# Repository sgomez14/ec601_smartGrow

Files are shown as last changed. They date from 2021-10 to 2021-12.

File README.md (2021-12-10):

# SmartGrow: Modular Smart Hydroponics System

## Problem:  Efficient Agriculture in a Worsening Climate
How can we efficiently bring agriculture indoors, so people can easily grow their own food?

## Solution
Take hydroponics, and make it smarter, scalable, and easily approachable.

## Users
Market: Scalable from a single person, to a  building, to a community.

## Societal Impact
Make self-sufficient farm more compact and accessible for urban communities.

Decreases food-waste, transit-fuel, land-use.

## Developers

| Name | Email |
| --- | --- |
| Santiago Gomez | santi09@bu.edu  |
| Ben Kuter | bmkuter@bu.edu  |
| Yuan Sui | suiyuan@bu.edu  |

## GrowPods

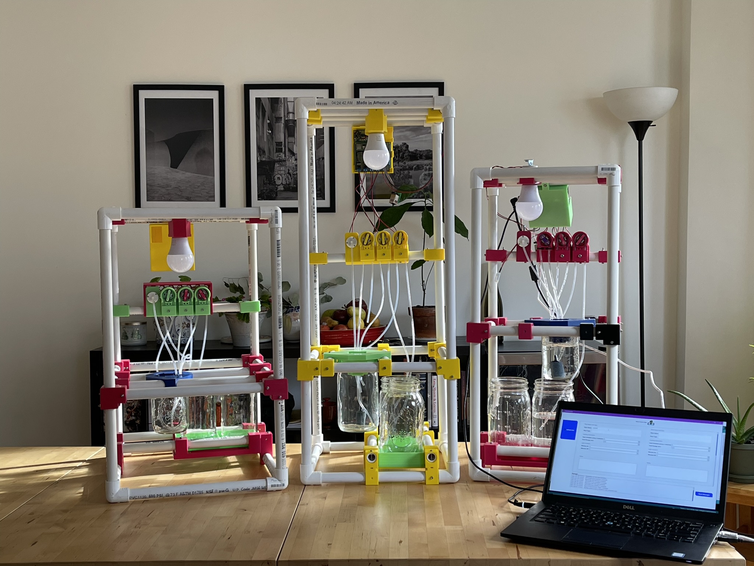
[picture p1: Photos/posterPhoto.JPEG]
GrowPods

Figure 1: Three Different Sized GrowPods

## GUI

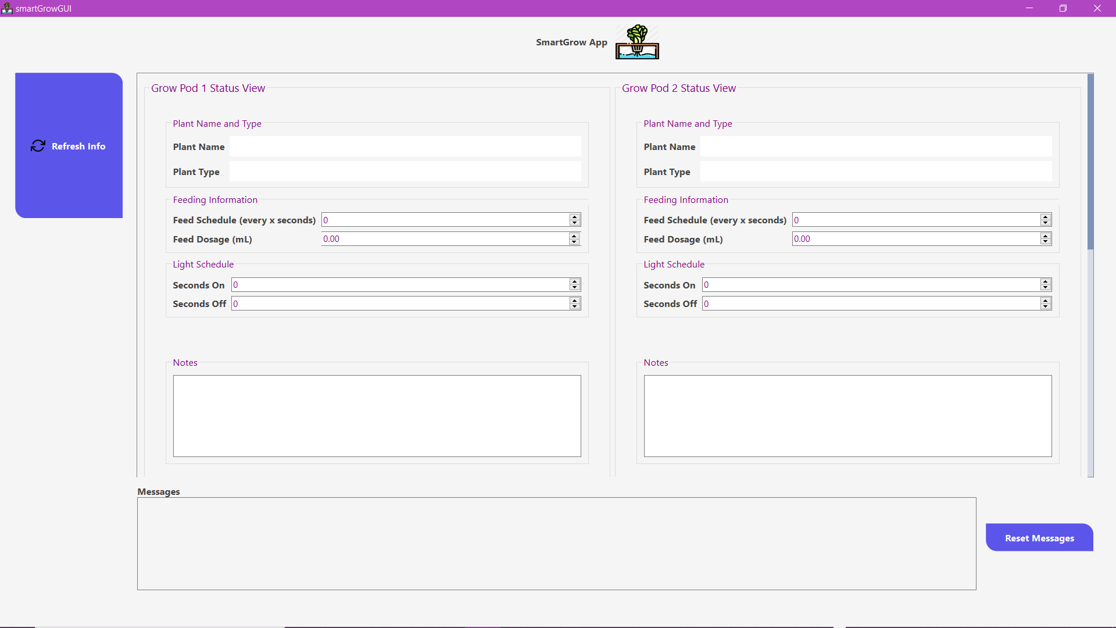
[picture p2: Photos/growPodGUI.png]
SmartGrow GUI

Figure 2: Smart GUI to Control GrowPods

## Functional Block Diagrams

### GrowPod Embedded System

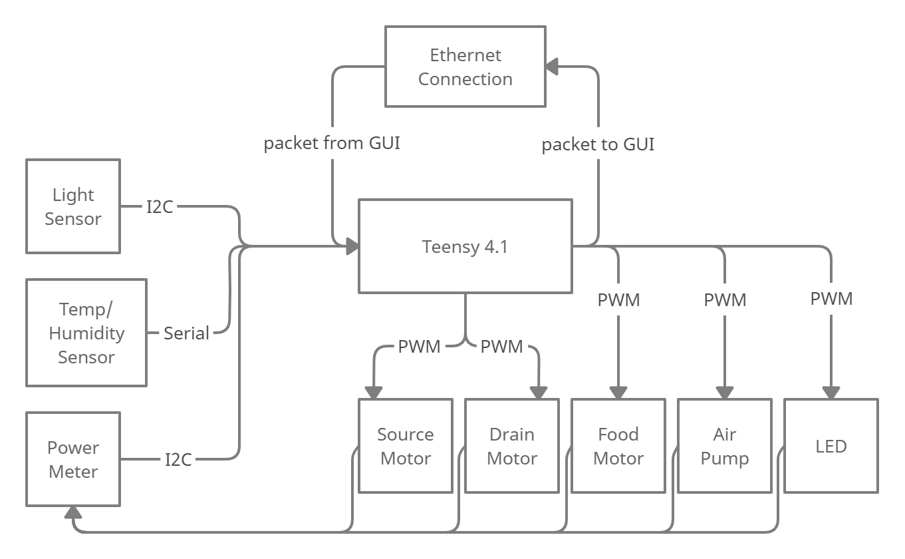
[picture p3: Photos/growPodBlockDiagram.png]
GrowPod Block Diagram

Figure 3: Block Diagram Explaining Embedded System Architecture

### UDP Communication Layer

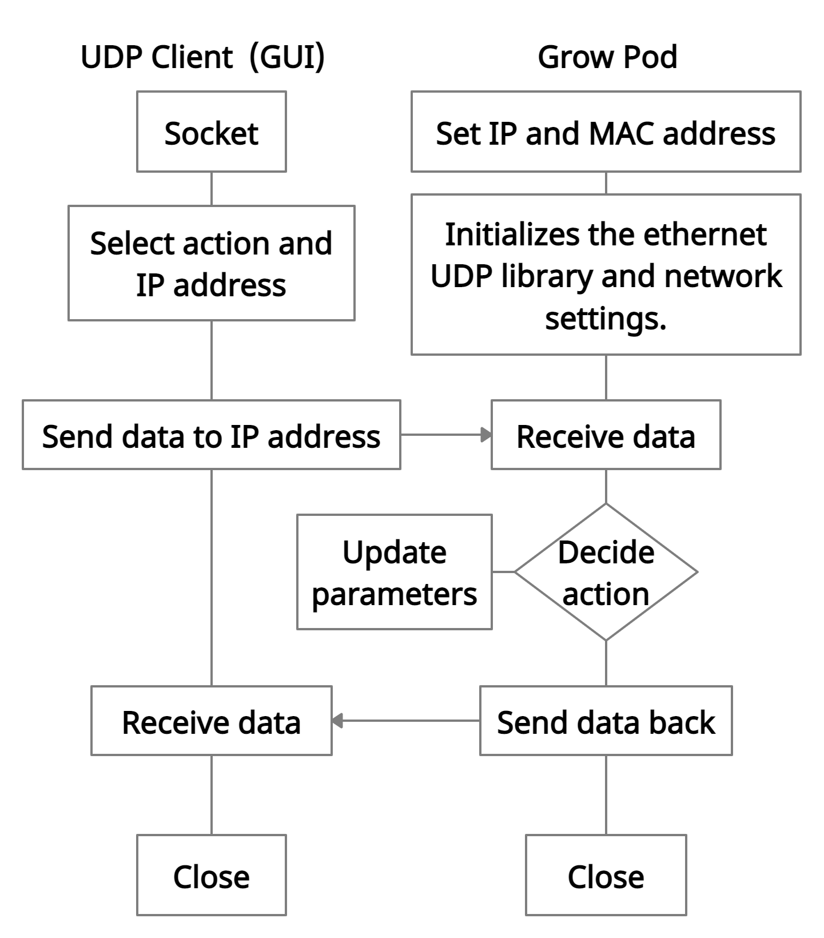
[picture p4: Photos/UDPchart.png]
UDP Block Diagram

Figure 4: Block Diagram Explaining UDP Communication Layer

## GrowPod Circuit

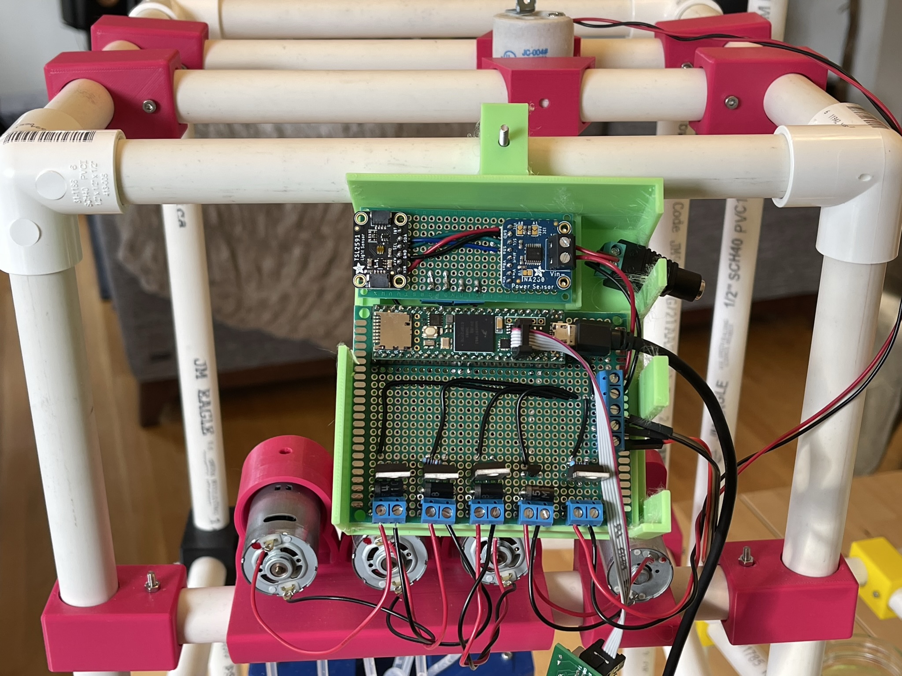
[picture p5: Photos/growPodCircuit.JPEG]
GrowPod Circuit Photo

Figure 5: Image of GrowPod Circuit

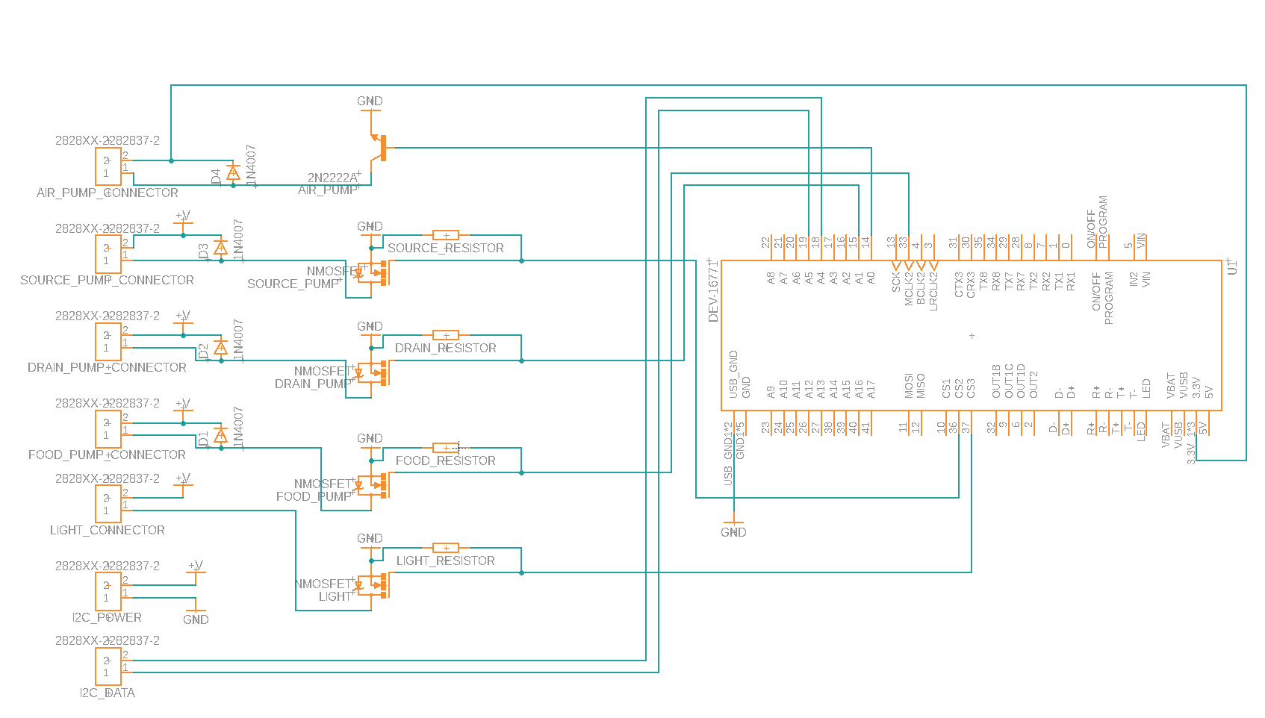
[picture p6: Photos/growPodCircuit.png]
GrowPod Circuit Diagram

Figure 6: Diagram of GrowPod Circuit

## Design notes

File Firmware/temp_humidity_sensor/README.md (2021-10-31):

# Temperature and Humidity Sensor README

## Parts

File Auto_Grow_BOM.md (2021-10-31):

**Benjamin Kuter**  
**EC601 - Fall 2021**  
**Automated Agricultural Grow System: Bill of Materials**  

<h2>pH Meter</h2>  
Probably one of the most expensive components that is the hardest to DIY, this costs ~$29 for V1 and ~$39 for V2. It is also fairly important to have for a hydroponics setup, since there is no soil to act as a buffer for the plant.  
*Link: https://www.dfrobot.com/product-1025.html*  

<h2>Teensy 4.1</h2>  
Brains of the operation. These are very powerful MCUs with very good support & programmability.  
*Link: https://www.pjrc.com/store/teensy41.html*  

<h2>Humidity & Temperature Sensor</h2>  
From Adafruit, the DHT22 is a low-cost digital temperature and humidity sensor. It can only poll data every couple of seconds, but for this application that is sufficient, especially considering the low price and ease of expanding larger modules with additional sensors.  
*Link: https://www.adafruit.com/product/385*  

<h2>Light Sensor</h2>  
VEML7700

<h2>Servos</h2>  
These are needed to open & close the drainage connections to each hydroponics unit, allowing water to be replaced within each module. The alternative would be another peristaltic pump, which may be too slow.  
*Link:  Product TBD*  

<h2>Peristaltic Liquid Pump</h2>
These will be used to safely (*following food safety regulations*) pump water from either the water reservoir to a module's hydroponics, or from the nutrient supply to the hydroponics chamber.    
*Link:  https://smile.amazon.com/gp/product/B01IUVHB8E/ref=ox_sc_saved_title_9?smid=A34K5WF5Z9R33P&psc=1*  
*Link: https://smile.amazon.com/gp/product/B08H1ZD5VZ/ref=ox_sc_saved_image_4?smid=A34K5WF5Z9R33P&psc=1*

<h2>Relays</h2>  
Numerous devices use 12v power, so a relay is needed to control these higher voltage devices.    
*Link:  https://smile.amazon.com/gp/product/B00KTELP3I/ref=ox_sc_saved_title_7?smid=A28RI4FXFS5SV8&psc=1*  

<h2>Grow Lights</h2>  
Once again, controlled via a relay. These could be replaced by higher quality alternatives, but for this project we are using standard A19 bulbs.  
*Link: https://smile.amazon.com/gp/product/B085ZVM2R7/ref=ox_sc_saved_image_2?smid=AWFJMAQAWVQZ0&psc=1*  
*Link: https://smile.amazon.com/gp/product/B07FMRLSWC/ref=ox_sc_saved_image_8?smid=A2C06C9V9JAET9&psc=1*  

<h2>HVAC</h2>  
This project assumes no odour control is needed. Airflow is still crucial for controlling humidity, temperature, and oxygen to root zones.  
*Link: TBD, probably computer fans I have around.*  

<h2>Humidifier</h2>
Exact product TBD, but something like this.  
*Link: https://smile.amazon.com/ToToT-5-Pack-Ultrasonic-Ceramics-Sealing/dp/B07RMX472R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*

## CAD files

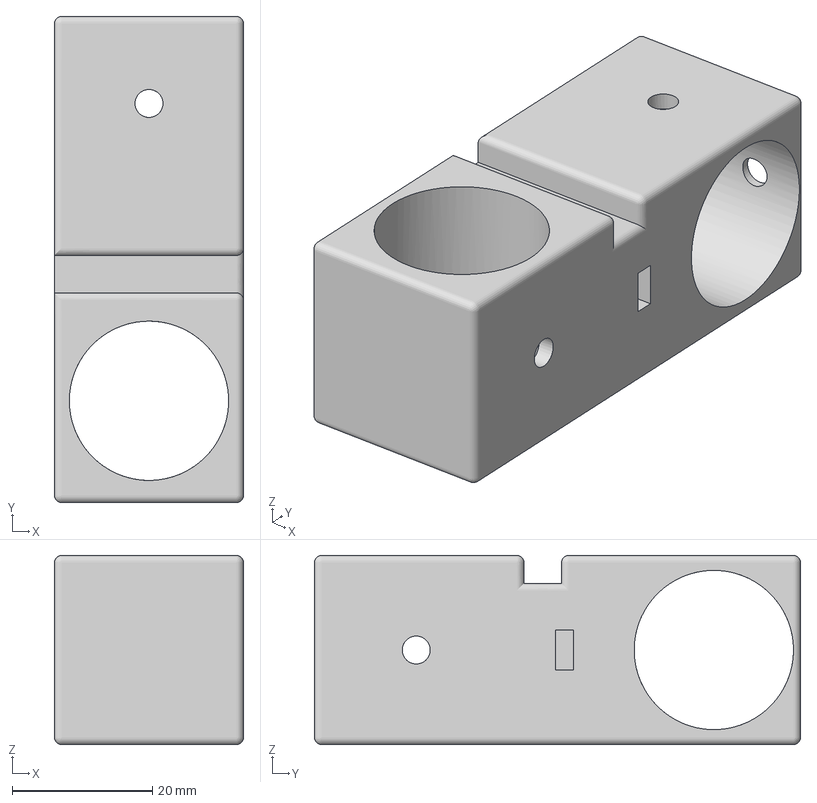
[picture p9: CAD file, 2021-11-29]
CAD/Stacked right.3mf
27.0 x 69.4 x 27.0 mm

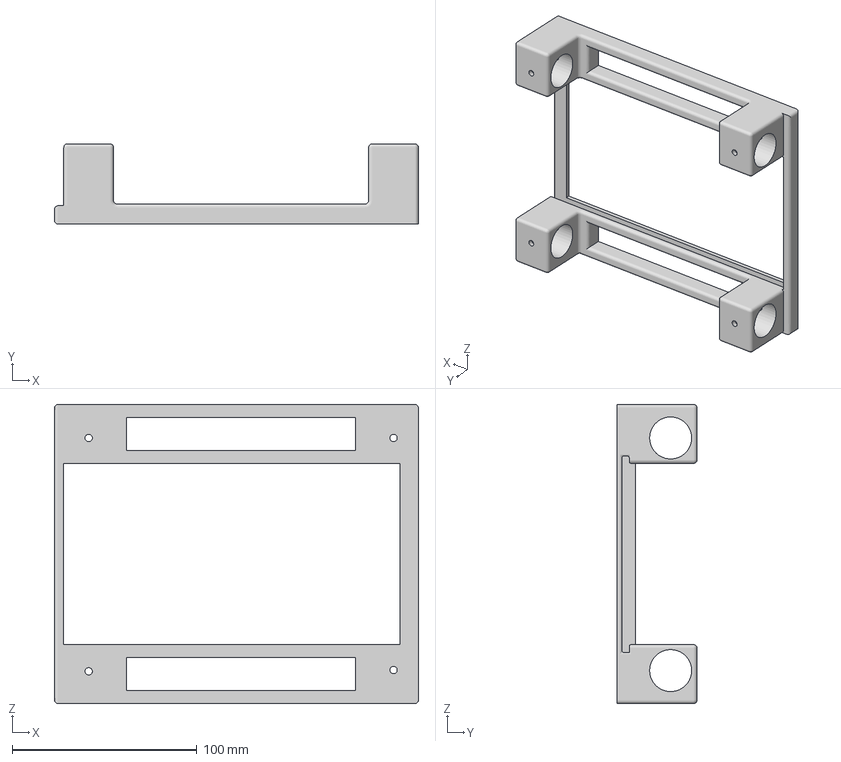
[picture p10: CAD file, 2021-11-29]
CAD/Bottom (1).3mf
197.0 x 43.5 x 162.0 mm

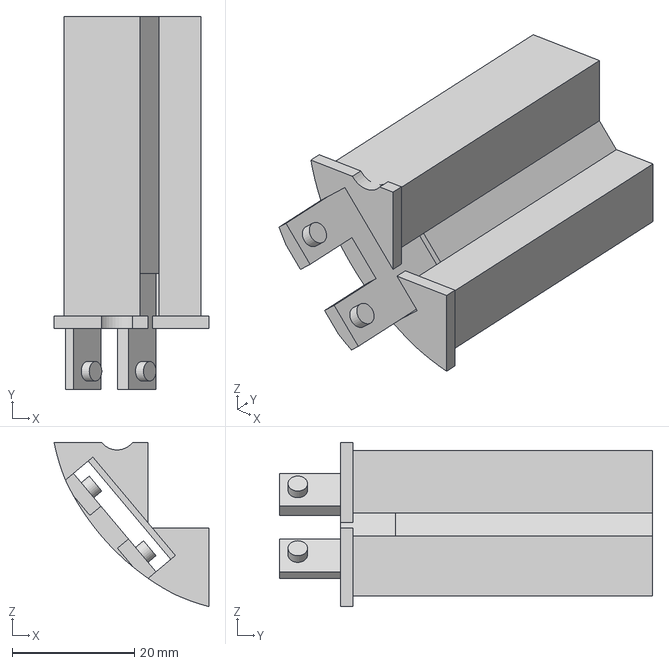
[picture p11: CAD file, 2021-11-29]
CAD/Water Sensor.3mf
25.3 x 61.0 x 26.9 mm

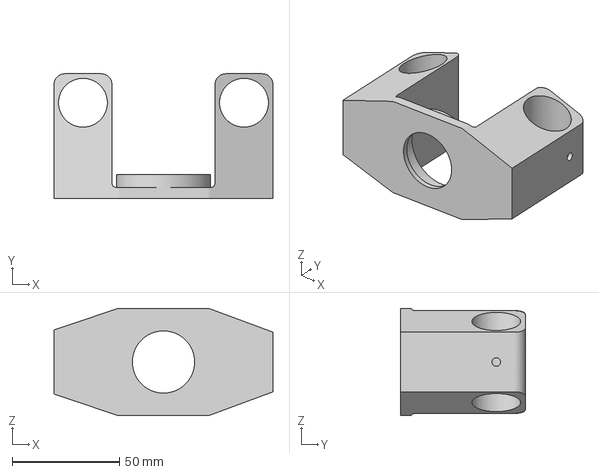
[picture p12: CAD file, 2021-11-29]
CAD/Light Fixture.3mf
102.0 x 58.0 x 50.0 mm

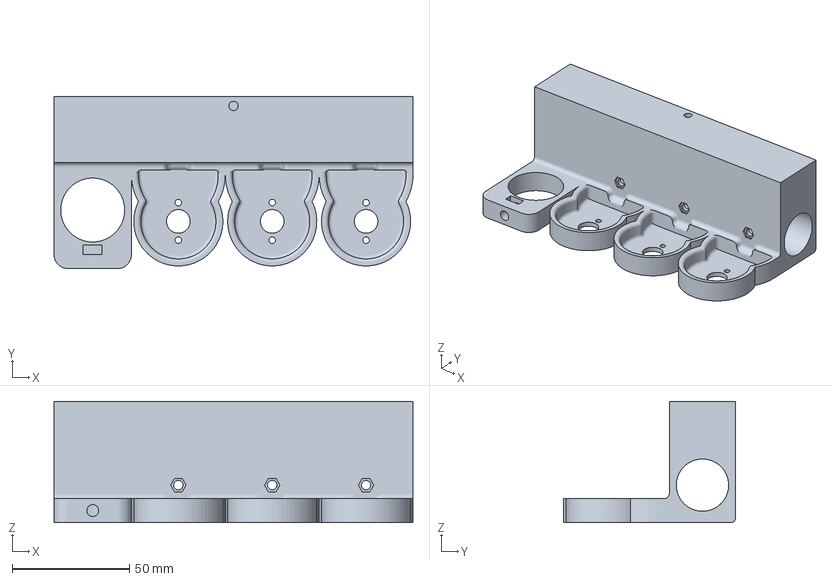
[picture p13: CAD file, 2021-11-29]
CAD/motor_mount.3mf
153.0 x 73.5 x 51.7 mm

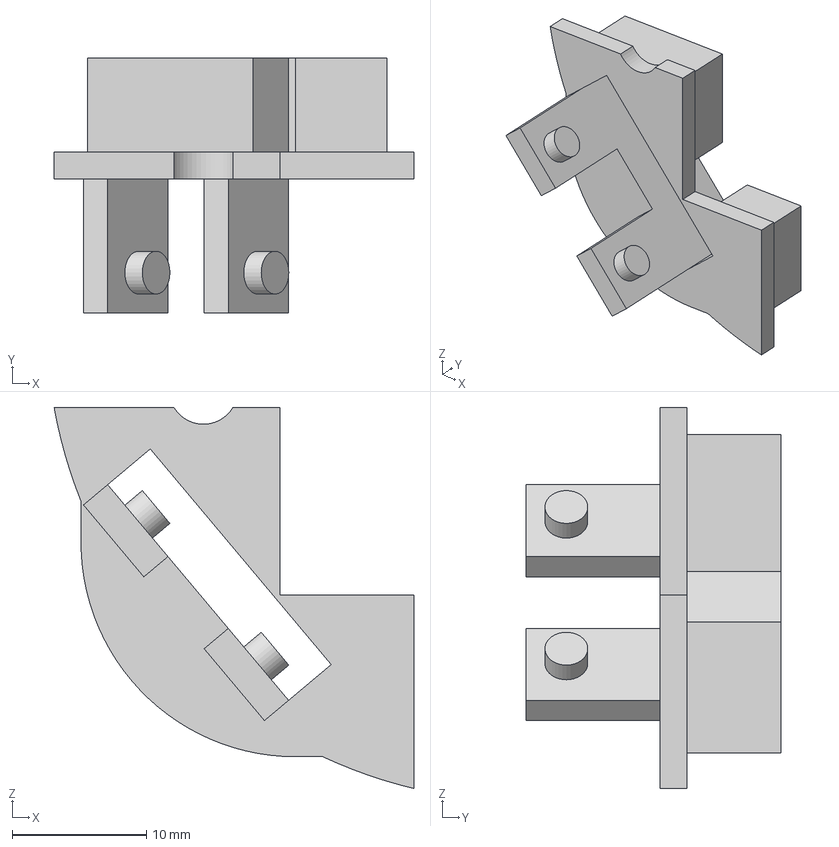
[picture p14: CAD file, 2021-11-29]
CAD/Water Sensor Block.3mf
26.8 x 19.0 x 28.4 mm

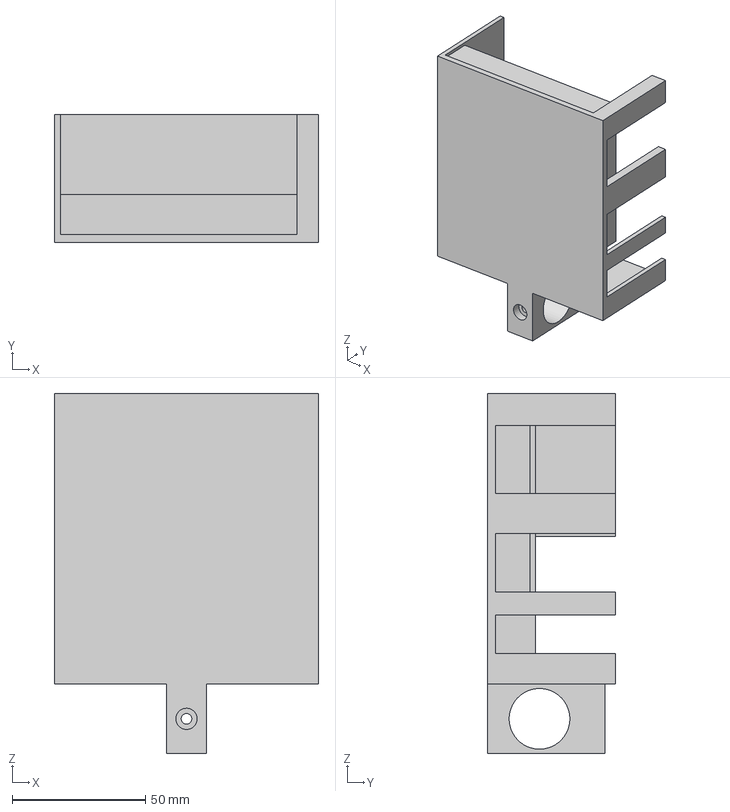
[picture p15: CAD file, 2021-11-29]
CAD/Body7.3mf
99.0 x 48.0 x 135.0 mm

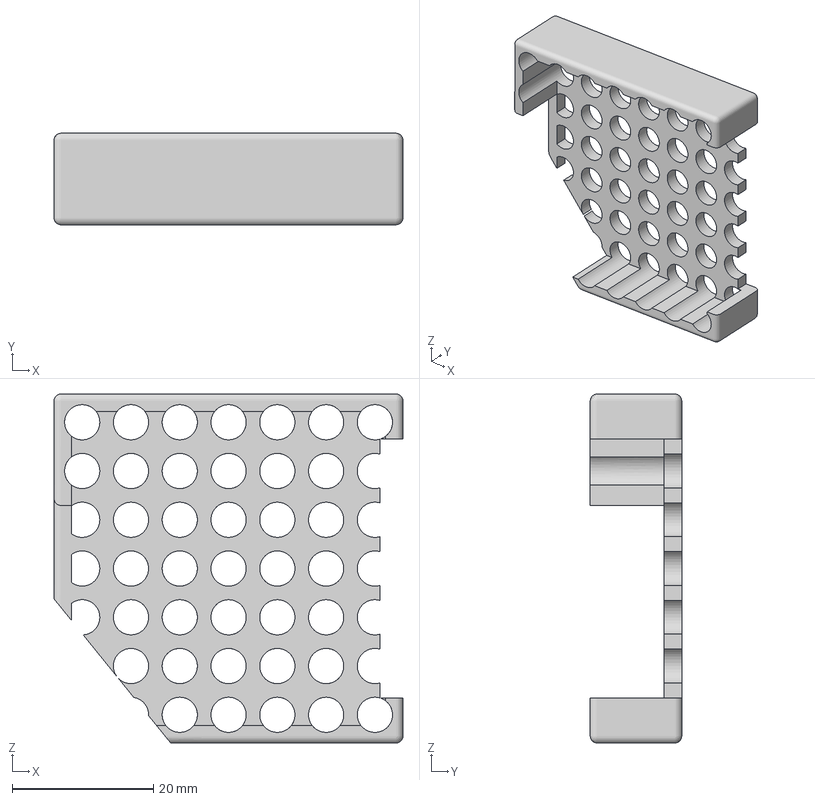
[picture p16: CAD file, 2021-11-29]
CAD/planter_lid.3mf
49.5 x 13.0 x 49.5 mm

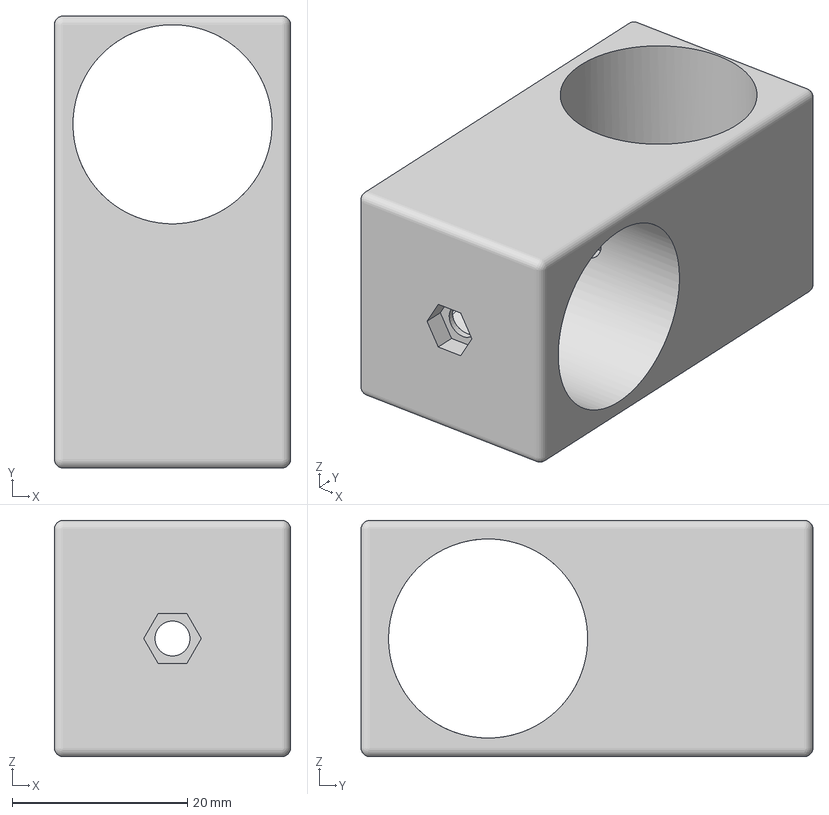
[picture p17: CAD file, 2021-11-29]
CAD/Stacked.3mf
27.0 x 51.6 x 27.0 mm

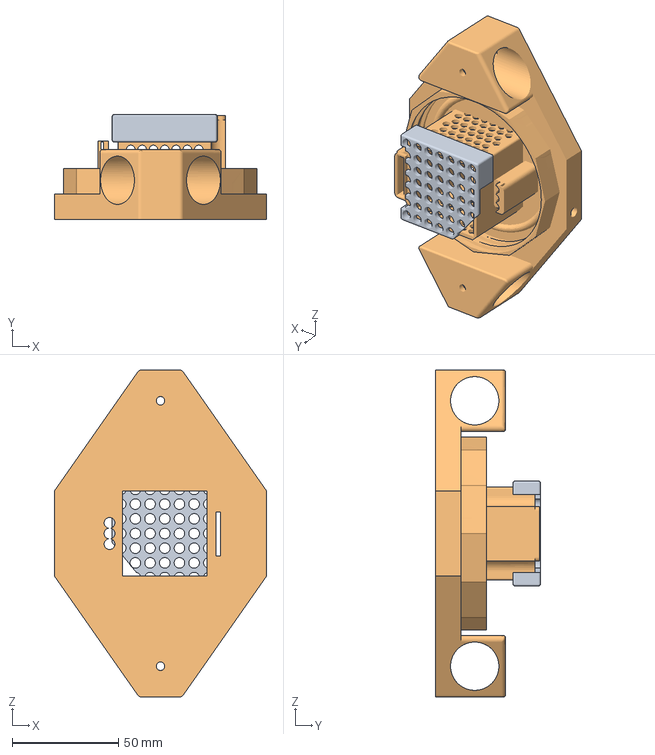
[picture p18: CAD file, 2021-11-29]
CAD/Planter.3mf
100.0 x 49.5 x 154.0 mm
planter

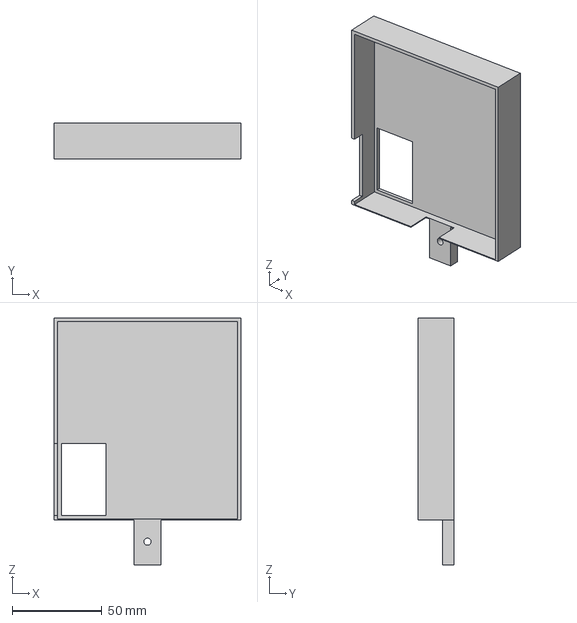
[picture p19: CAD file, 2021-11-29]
CAD/Top.3mf
104.0 x 20.0 x 137.5 mm

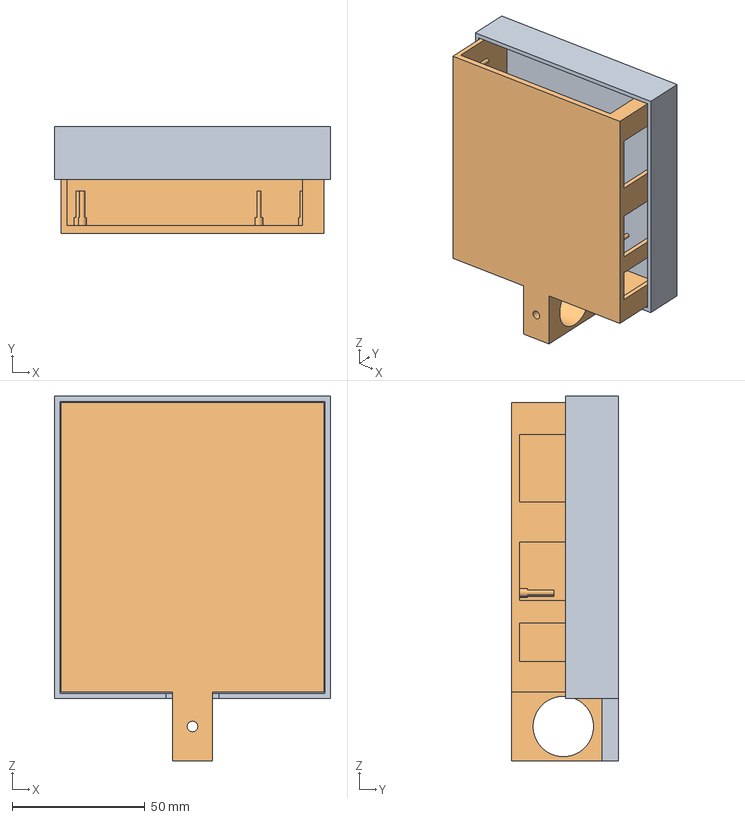
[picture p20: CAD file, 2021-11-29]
CAD/PCB case.3mf
104.0 x 40.2 x 137.5 mm

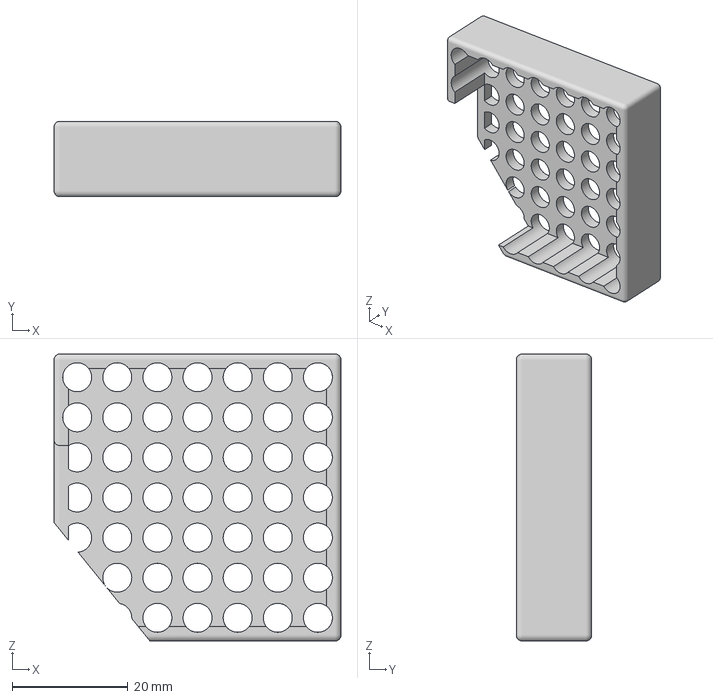
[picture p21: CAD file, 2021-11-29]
CAD/Grow Lid.3mf
49.5 x 13.0 x 49.5 mm

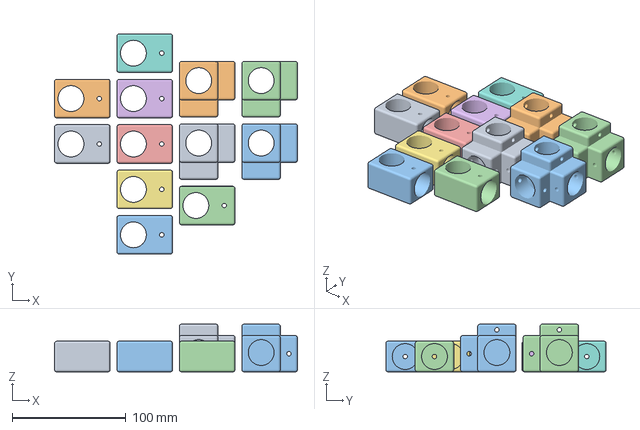
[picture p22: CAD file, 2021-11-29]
CAD/Tube arm.3mf
214.0 x 194.0 x 42.0 mm
Corner
Middle

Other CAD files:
CAD/Stacked left.3mf
CAD/Drawer.3mf
CAD/Flywheel.3mf
CAD/Body9.3mf
CAD/3mm x 4mm Adapter.3mf
CAD/4 Motor Mount.3mf
CAD/Air Pump Base.3mf
CAD/Balance Wheel.3mf
CAD/Base.3mf
CAD/Body8.3mf
CAD/Bottom Frame (2) (1).3mf
CAD/Bottom Frame (2).3mf
CAD/Bottom Frame Knurled.3mf
CAD/Bottom Wheel (2).3mf
CAD/Centrifugal Air Pump.3mf
CAD/Impeller.3mf
CAD/Middle.3mf
CAD/Motor Enclosure.3mf
CAD/Motor Mount V2.3mf
CAD/PVC jig.3mf
CAD/Planter.stl
CAD/Top Frame (2).3mf
CAD/Top Wheel (2) (1).3mf
CAD/Top Wheel (2).3mf
CAD/Tray.3mf
CAD/Water Pump.3mf
CAD/air_pump_mount.3mf
CAD/lid.3mf
CAD/mirrored_bottom_wheel.3mf
CAD/planter (1).3mf

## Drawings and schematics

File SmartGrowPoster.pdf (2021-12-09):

# SmartGrow: Modular Automated Hydroponics Growing System

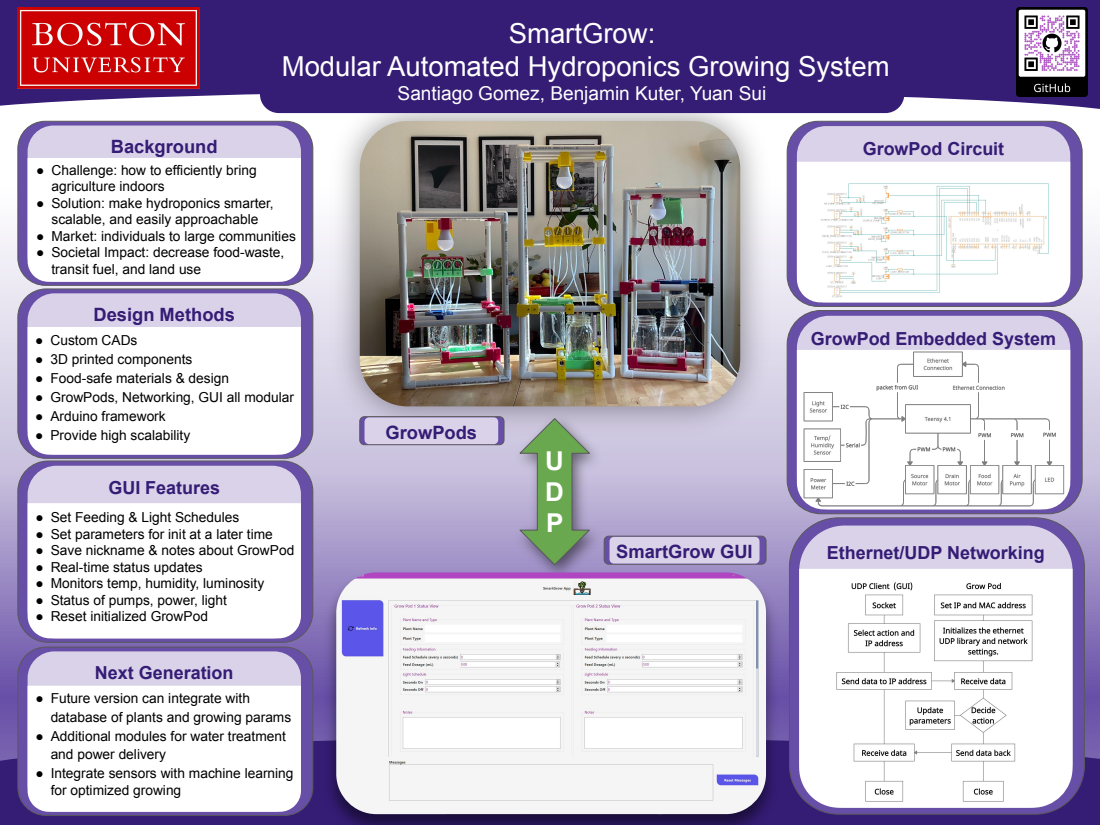
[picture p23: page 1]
Background; Design Methods; GUI Features; Next Generation; GrowPod Circuit; GrowPods; SmartGrow GUI

Santiago Gomez, Benjamin Kuter, Yuan Sui

● Challenge: how to efficiently bring
agriculture indoors
● Solution: make hydroponics smarter,
scalable, and easily approachable
● Market: individuals to large communities
● Societal Impact: decrease food-waste,
transit fuel, and land use

GrowPod Embedded System

● Custom CADs
● 3D printed components
● Food-safe materials & design
● GrowPods, Networking, GUI all modular
● Arduino framework
● Provide high scalability

● Set Feeding & Light Schedules
● Set parameters for init at a later time
● Save nickname & notes about GrowPod
● Real-time status updates
● Monitors temp, humidity, luminosity
● Status of pumps, power, light
● Reset initialized GrowPod

Ethernet/UDP Networking

● Future version can integrate with
database of plants and growing params
● Additional modules for water treatment
and power delivery
● Integrate sensors with machine learning
for optimized growing

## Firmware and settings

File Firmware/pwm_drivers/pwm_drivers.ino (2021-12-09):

/*
 Name:		Smart_Grow.ino
 Created:	10/7/2021 7:58:56 PM
 Author:	bmk

 Notes:
 Motor & MOSFET Wiring: https://www.youtube.com/watch?v=3PkpOeHTnfo
 Air Pump: https://www.youtube.com/watch?v=nGVykVrly9g


*/

#include "pwm_functions.h"

EthernetServer server(80);

void setup() {
	Serial.begin(9600);

	
#if DEBUG
	while (!Serial) {
		; // wait for serial port to connect. Needed for native USB
	}
#endif

	if (tsl.begin())
	{
		Serial.println(F("Found a TSL2591 sensor"));
	}
	else
	{
		Serial.println(F("No sensor found ... check your wiring?"));
		while (1);
	}
	
	if (!ina260.begin()) {
		Serial.println("Couldn't find INA260 chip");
		while (1);
	}
	else
	{
		Serial.println("Found INA260 chip");
	}
	
	teensyMAC(mac);

	/* Start networking */	
#if ETHERNET
	Serial.println("Begin ethernet");
	Ethernet.begin(mac, device_ip);
	Serial.println("Begin UDP");
	Udp.begin(local_port);
	server.begin();
	Serial.print("server is at ");
	Serial.println(Ethernet.localIP());
#endif // ETHERNET

#if DEBUG
	Serial.println("Entering debug loop: ");
	/*
	PWM_calibration(&air_pump);
	PWM_calibration(&water_pump_source);
	PWM_calibration(&water_pump_drain);
	PWM_calibration(&food_pump);
	PWM_calibration(&LED);
	*/
	while (1) 
	{ 
		Serial.println("In debug loop: ");
		PWM_set_percent(&water_pump_source, 100);
		delay(30000);
		PWM_set_percent(&water_pump_source, 0);
		PWM_set_percent(&water_pump_drain, 80);
		delay(30000);
		PWM_set_percent(&water_pump_drain, 0);
		PWM_set_percent(&food_pump, 100);
		delay(2000);
		PWM_set_percent(&food_pump, 0);
	}
#endif

	Serial.println("Init temp sensor");
	tempSensorInit();

	Serial.println("Init light sensor");
	init_light_sensor();

	//initialize();

	Serial.println("Initial 2 sec delay:");
	delay(2000);



	pinMode(13, OUTPUT);
	pinMode(LED.pin, OUTPUT);
	digitalWrite(13, HIGH);
	pinMode(DHTPIN, INPUT);
}
 
// the loop function runs over and over again until power down or reset
void loop() {
	//Serial.println("Top of loop");
	//print_ethernet_test();
	if (system_attention_flag)
	{
		Serial.printf("ERROR IN SYSTEM. CURRENT OVERDRAW PROTECTION ACTIVATED. CHECK FOR PUMP JAMS.\n");
		reset();
	}
	else
	{
		/* Receive command packet*/
		get_packet();

		/* Scheduler */
		scheduler();

		/* Send response packet*/
		send_packet();

		/* Printing timers for debugging */
#if DEBUG
		Serial.print("change_water: ");
		Serial.println(change_water);
		Serial.print("turn_off_light: ");
		Serial.println(turn_off_light);
		Serial.print("turn_on_light: ");
		Serial.println(turn_on_light);
		Serial.println();
#endif

	}
	//Serial.printf("Light Status: %d\n", LED_status);
	//Serial.printf("Light ON: %u\nLight OFF: %u\n", turn_on_light_threshold, turn_off_light_threshold);
	delay(200);
}

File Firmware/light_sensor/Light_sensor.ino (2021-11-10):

/*
 Name:    Light_sensor.ino
 Author:  Yuan
 Notes:
 TSL2591 example code form https://learn.adafruit.com/adafruit-tsl2591/wiring-and-test
*/

#include "lightsensor.h"


void setup(void) 
{
  Serial.begin(9600);
  /* Initial the sensor */
  
  init_light_sensor();
  light_sensor_init_info();

}

void loop(void) 
{  
  if(read_light_data()){
    print_light_data();
    delay(500);
  }
  else{
    Serial.println(F("Wrong light data"));
  }

}

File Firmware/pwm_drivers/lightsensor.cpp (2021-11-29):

#include "lightsensor.h"

Adafruit_TSL2591 tsl = Adafruit_TSL2591(2591);

void light_sensor_init_info(void)
{
  /* Display the gain and integration time for reference*/  
  Serial.println(F("------------------------------------"));
  Serial.print  (F("Gain:         "));
  tsl2591Gain_t gain = tsl.getGain();
  switch(gain)
  {
    case TSL2591_GAIN_LOW:
      Serial.println(F("1x (Low)"));
      break;
    case TSL2591_GAIN_MED:
      Serial.println(F("25x (Medium)"));
      break;
    case TSL2591_GAIN_HIGH:
      Serial.println(F("428x (High)"));
      break;
    case TSL2591_GAIN_MAX:
      Serial.println(F("9876x (Max)"));
      break;
  }
  Serial.print  (F("Timing:       "));
  Serial.print((tsl.getTiming() + 1) * 100, DEC); 
  Serial.println(F(" ms"));
  Serial.println(F("------------------------------------"));
  Serial.println(F(""));
}

void init_light_sensor(void){
 /* 
  Set Gain option:
  TSL2591_GAIN_LOW  // 1x gain (bright light)
  TSL2591_GAIN_MED  // 25x gain
  TSL2591_GAIN_HIGH // 428x gain

  Set Timing option:
  TSL2591_INTEGRATIONTIME_100MS  // shortest integration time (bright light)
  TSL2591_INTEGRATIONTIME_200MS
  TSL2591_INTEGRATIONTIME_300MS
  TSL2591_INTEGRATIONTIME_400MS
  TSL2591_INTEGRATIONTIME_500MS
  TSL2591_INTEGRATIONTIME_600MS  // longest integration time (dim light)
*/

  tsl.setGain(TSL2591_GAIN_MED); 

  tsl.setTiming(TSL2591_INTEGRATIONTIME_300MS);

}


void print_light_data(void)
{
  // Read 32 bits with top 16 bits IR, bottom 16 bits full spectrum
  uint32_t lum = tsl.getFullLuminosity();
  uint16_t ir, full;
  ir = lum >> 16;
  full = lum & 0xFFFF;
  Serial.print(F("[ ")); Serial.print(millis()); Serial.print(F(" ms ] "));
  Serial.print(F("IR: ")); Serial.print(ir);  Serial.print(F("  "));
  Serial.print(F("Full: ")); Serial.print(full); Serial.print(F("  "));
  Serial.print(F("Visible: ")); Serial.print(full - ir); Serial.print(F("  "));
  Serial.print(F("Lux: ")); Serial.println(tsl.calculateLux(full, ir), 6);
}

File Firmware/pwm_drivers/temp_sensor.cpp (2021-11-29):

/*
     Name:		temp_sensor.cpp
     Created:	10/22/2021 12:48:59 PM
     Author:	Santiago Gomez, santi09@bu.edu

    Temp/Humidity Sensor Firmware Adapted from Tutorial Below

    Arduino example code for DHT11, DHT22/AM2302 and DHT21/AM2301 temperature and humidity sensors.
    More info: www.www.makerguides.com/dht11-dht22-arduino-tutorial
*/

#include "temp_sensor.h"

// Initialize DHT sensor for normal 16mhz Arduino:
DHT tempSensor = DHT(DHTPIN, DHTTYPE);

// Initialize temperature data structure
tempSensorData tempData = { 0,0,0,0,0 };

// Wrapper function that reads humidity, temp, and heat index
// returns bool indicating if reading the sensor was successful
// pass in pointers to sensor object and sensor data structure
bool readTempSensor(DHT* dhtSensor, tempSensorData* tempData)
{
    // Reading temperature or humidity takes about 250 milliseconds!
    // Sensor readings may also be up to 2 seconds 'old' (its a very slow sensor)

    // Read the humidity in %:
    tempData->humidity = dhtSensor->readHumidity();

    // Read the temperature as Celsius:
    tempData->celcius = dhtSensor->readTemperature();

    // Read the temperature as Fahrenheit:
    tempData->fahrenheit = dhtSensor->readTemperature(true);

    // Check if any reads failed and exit early (to try again):
    if (isnan(tempData->humidity) || isnan(tempData->celcius) || isnan(tempData->fahrenheit)) {

        //reset tempData values
        tempData->humidity = 0;
        tempData->fahrenheit = 0;
        tempData->celcius = 0;
        tempData->heatIndex_F = 0;
        tempData->heatIndex_C = 0;
        return false;
    }

    // Compute heat index in Fahrenheit (default):
    tempData->heatIndex_F = dhtSensor->computeHeatIndex(tempData->fahrenheit, tempData->humidity);

    // Compute heat index in Celsius:
    tempData->heatIndex_C = dhtSensor->computeHeatIndex(tempData->celcius, tempData->humidity, false);

    return true;
}

// Function for printing sensor data
void printTempData(tempSensorData* tempData)
{
    Serial.print("Humidity: ");
    Serial.print(tempData->humidity);
    Serial.print(" % ");
    Serial.print("Temperature: ");
    Serial.print(tempData->celcius);
    Serial.print(" \xC2\xB0");
    Serial.print("C | ");
    Serial.print(tempData->fahrenheit);
    Serial.print(" \xC2\xB0");
    Serial.print("F ");
    Serial.print("Heat index: ");
    Serial.print(tempData->heatIndex_C);
    Serial.print(" \xC2\xB0");
    Serial.print("C | ");
    Serial.print(tempData->heatIndex_F);
    Serial.print(" \xC2\xB0");
    Serial.println("F");
}

void tempSensorInit(void)
{
    // Initialize sensor
    tempSensor.begin();
}

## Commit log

2021-10-31 Upload CAD folder
    [4 Motor Mount.3mf, Base.3mf, Bearings.3mf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]
2021-10-31 Added light sensor folder
2021-10-31 Added Power Sensor folder
2021-10-31 Added Temp/Humidity Sensor folder
2021-10-31 Adding tempSensor firmware v1
    created h and cpp files that implement the temperature/humidity sensor. Also created arduino file that tests the temp sensor firmware.
2021-11-04 Adding CAD files and cleaning up folder.
    [3mm x 4mm Adapter.3mf, 4 Motor Mount.3mf, Air Pump Base.3mf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]
2021-11-04 Adding PWM functions
2021-11-06 Updating for code review
    [Motor Mount V2.3mf, Water Pump.3mf]
2021-11-06 Putting tempSensor firmware in correct folder
    [TempHumiditySensor.ino]
2021-11-06 renaming pwm folder for testing
    [Motor Mount V2.3mf]
2021-11-06 Updating firmware location for temp sensor
2021-11-07 update sensor include file name
2021-11-16 created initial framework for GUI
2021-11-19 Adding a few more functions.
    [Bottom (1).3mf]
2021-11-22 adding UDP functions
    [lid.3mf]
2021-11-22 Changed output buffer to be based on sprintf()
    [motor_mount.3mf]
2021-11-24 Current protection code
2021-11-26 Added Timers and Parsing Incoming MCU Packet
2021-11-28 string parsing
    [Body7.3mf, Bottom Frame (2) (1).3mf, Flywheel.3mf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]
2021-11-29 Update Tube arm.3mf
    [Tube arm.3mf]
2021-12-02 firmware updated to work with GUI, GUI now handles failed UDP packets
    [pwm_drivers.ino, pwm_functions.cpp]
2021-12-10 changed timer to every 5 minutes
